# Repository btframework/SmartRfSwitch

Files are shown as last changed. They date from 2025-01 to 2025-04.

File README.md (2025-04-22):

# Smart RF Switch

 **Required Hardware**
 - 433Mhz RF switch and relay set
 - ESP32C4FN Super Mini
 
 **Required Arduino Libraries**
 - esp32 by Espressif Systems (board) 3.2.0
 - HomeSpan 2.1.1
 
 **Arduino IDE Settings**
 - Board: ESP32C3 Dev BModule
 - ESP CDC On Boot: Enabled
 - CPU Frequency: 80MHz (WiFi)
 - Core Debug Level: None
 - Erase All Flash Before Sketch Upload: Disabled
 - Flash frequency: 80Mhz
 - Flash Mode: QIO
 - Flash Size: 4MB (32Mb)
 - JTAG Adapter: Disabled
 - Partition Scheme: Huge APP (3MB No OTA/1MB SPIFFS)
 - Upload Speed: 921600
 - Zigbee Mode: Disabled
 - Programmer: Esptool

This repository contains firmware for the HomeKit device described in [this video](https://youtu.be/C4awq37Im1w).

## 433Mhz RF Switch to HomeKit connection
   
  Smart light bulbs, smart relays, and other “smart” devices in the home are cool. But! There's always that damn “but.” At 3 a.m., when everyone is asleep, yelling, “Hey Siri! Turn on the kitchen light” is not a good idea. And constantly reaching for your smartphone to turn something on or off is also not a good idea. You can, of course, put motion sensors in, but there are nuances with them. So you can't do without switches.

  My first impulse was to buy a switch that is compatible with my smart home system (and I have an Apple Home, mind you). I looked at what was on sale. First of all, most are from the Chinese and required their own application that somehow cleverly threw something there somewhere. Secondly, which is quite sad, most required a prepared wiring or ZigBee gateway, or both. In general, the option fell away for several reasons.

  The second thought (which comes later) was to buy any switch at all and wire it to the Apple Home via HomerBridge. This idea again ran into ZigBee hubs and wiring.

  Having given up on all this nonsense and racking my brains, I suddenly remembered that I'm a programmer. What should we do to make a switch ourselves? No problem. We take a radio relay and build it. I stalled on the fact that I was too lazy to print a normal switch button. So the idea was put aside in not a very long.

  So, not too long ago, I was looking for something online and decided to see what's out there in the smart switch technology realm. And I found a cool thing: a full-size switch with a relay on 433 MHz. And the main thing is that this switch (the button itself) works from a battery, and the relay is connected to the wires of the chandelier (or bulb). Thus, special wiring for it is not needed.

  > Let me make it clear: by “special wiring”, I mean phase and zero wiring to the light switch. That is, you should have three wires coming to the switch: phase from the switchboard (which is broken), phase to the chandelier, and zero from the switchboard. Usually, the standard wiring to the switch is just two wires: phase from the switchboard, and it goes to the chandelier (phase break). There is no zero there.

  Here is the switch.

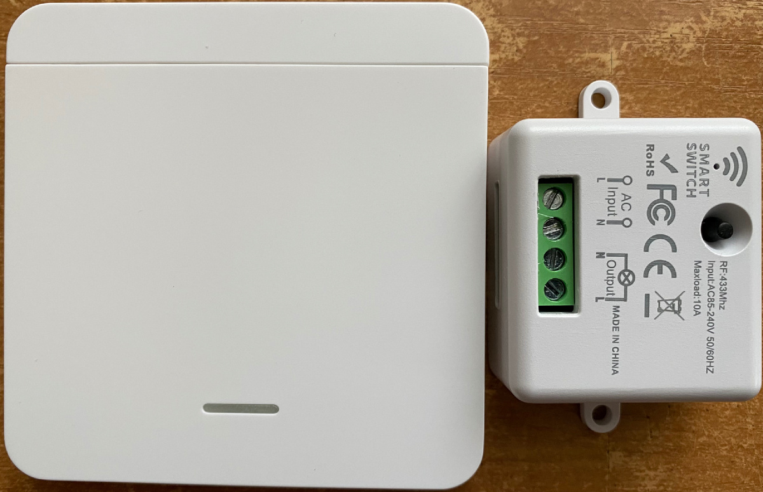
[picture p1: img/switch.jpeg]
RF Switch
  

  The only thing left to do is to make this switch compatible with Apple Home. Naturally, I will use the ESP32 in conjunction with the Arduino HomeSpan library. I have been friends with this library for a long time, and I already have devices made on its basis. Yes, and the experience of the “adaptation” radio call (also on 433) I already had. No problems were expected.

  Before breaking the relay, I looked in the manual. And there I found a mention that more than one button can be attached to the relay. Interesting, I thought, so the buttons are different somehow. Well, it's time to open this marvelous device of Chinese industry. The button is of little interest to me; it's just an ordinary RF transmitter. It works, and it's good. But the relay should be studied in detail. The case is not glued, not sealed, and in general, it opens easily. Here's what I got out of this white box.

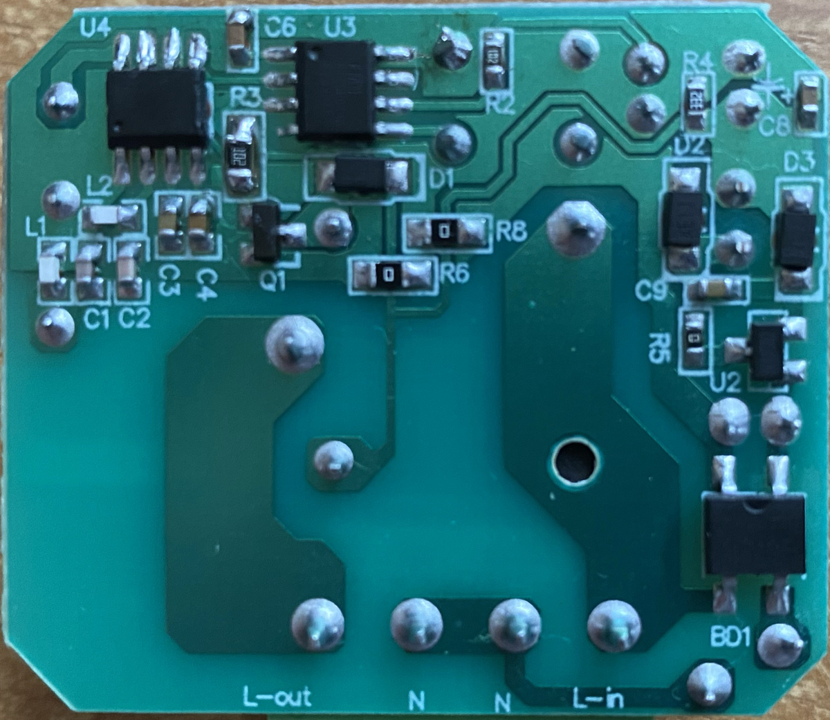
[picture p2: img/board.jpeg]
RF Switch Board
  

  In the right part of the board, you can see a transformerless (you should take note of it!) power supply assembled on diode bridge BD1. Some microcircuit U2 (I suspect it is a stabilizer for some volts) with marking IVAP302 (couldn't find what it is; if you know what it is, please write in comments), diodes D2 and D3, and some stuff (capacitors, resistors). Several elements are not labeled and soldered on the back side of the board. In particular: a ballast resistor and a couple of smoothing capacitors. All in all, nothing interesting. The only thing that interested me here is the stabilizer. Since it determines the supply voltage of the rest of the circuit and, as a consequence, the options for matching it (the circuit) with ESP32. You can stupidly measure the output voltage from the power supply, and then you can figure it out by indirect signs. I decided on the second option because I still need to find out the “protocol” of communication between the button and the relay.

  In the left part of the board there is the relay control circuit itself, consisting of two microcircuits, U4 (the name is lost) and U3 (marking FMD FT60E011A F269RKE), some loose parts, transistor Q1, and, actually, the relay itself. Relay marking: BRD-SS-105LMF. And this indicates that the relay is a five-volt relay. Which is very good and hints that the circuit works from 5 volts. Of course, it is not certain that the rest of the circuit is powered by five volts, since the relay is switched through a transistor, but it is something. It's unlikely to be more than that.

  A quick Google search for FT60E011A gives us a link to a data sheet that shows that this is a simple microcontroller. This is also indicated by the fact that to this chip (U3) are connected the button, the LED, the base of transistor Q1 (via current-limiting resistor R3), and the second chip (U4). Hence, U4 is an RF chip. And it transmits the received signal to the microcontroller. In this case I am not interested in the RF chip itself and its piping, so I will not describe what is there and how. It's just a bunch of capacitors and an antenna.

  > Transistor Q1 in this circuit works as a key: it allows a small current from the microcontroller to control a relatively large relay winding current. Usually microcontroller outputs are designed for currents of a couple of tens of milliamperes. But the relay itself consumes much more current (it can even reach hundreds of milliamperes). The microcontroller will simply not be able to deliver such current to its outputs. And if it can, it is very likely to burn out. This is why a transistor key is used. Well, diode D1 dampens the reverse energy discharge from the relay coil.

  Now I need to figure out what exactly the RF chip sends to the microcontroller and how the microcontroller controls the relay. I'll look at the signal levels as well. It's time to poke around with an oscilloscope.

  Before poking with oscilloscope probes, we should solve the problem with the power supply. I don't really want to get into the device, which is directly powered from 220 without isolation. I decided to supply power directly after the diode bridge from a laboratory power supply unit. It started from 12 volts.

  Signal from the RF chip to the IC without a button command. Occasionally there's some interference. But it's mostly quiet.

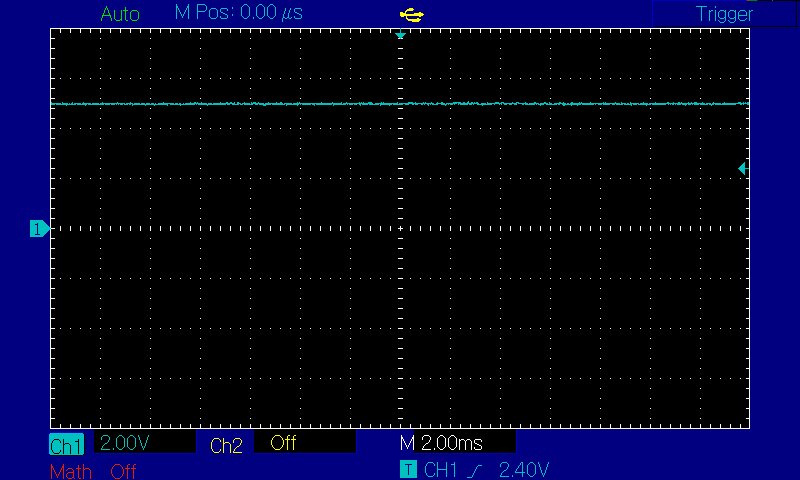
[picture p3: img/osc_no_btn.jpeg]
Oscillogram without button pressed
  

  If you press the button, the RF chip starts transmitting something to the microcontroller. I suspect it is the code of the button.

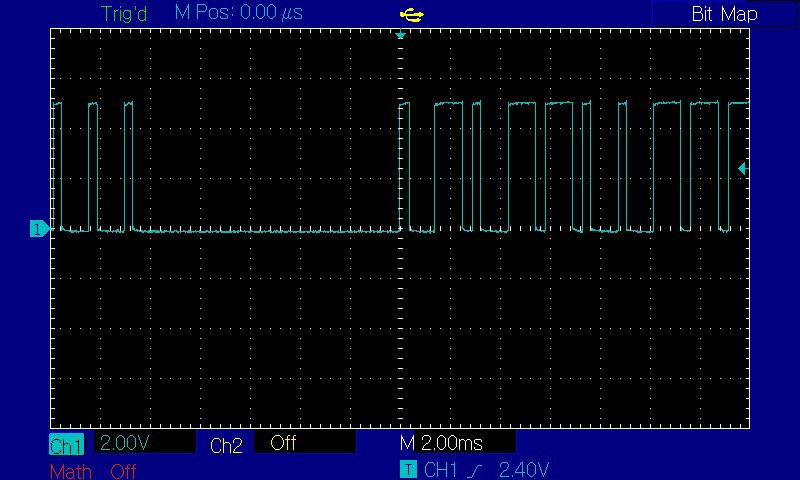
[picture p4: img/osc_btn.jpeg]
Oscillogram with button pressed
  

  The screenshot doesn't show everything, but it's a pretty long sequence. You can immediately see that the signal has a 5-volt level, which is very, very good. Well, and the relay is 5 volts, as I mentioned above. So there will be no problems with level matching.

  I didn't really want to decode and emulate the signal, so I also looked at the relay control signal (on R3 on the microcontroller side). I will not give the oscillogram; everything is expected there. Either constantly high level (5 volts) when the relay is turned on (closes the output contacts). Or constantly low when the output is open.

  In general, I decide to connect to the gap between the microcontroller and Q1. To do this, it will be necessary to unsolder resistor R3. I have sketched this connection diagram.

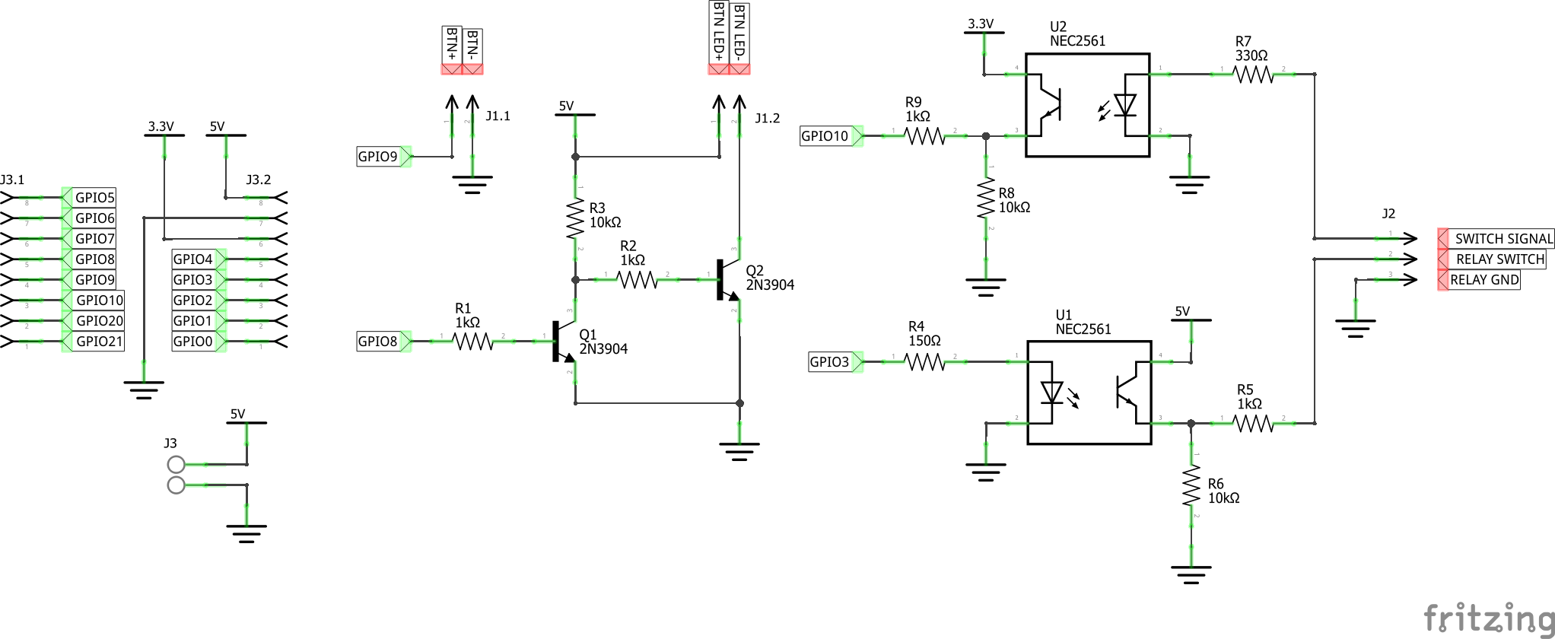
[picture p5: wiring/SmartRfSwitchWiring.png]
Wiring diagram
  

  According to the scheme, everything is very simple. Opto isolation from the relay (since I remember that there is a transformerless power supply, which has no galvanic isolation from the 220-volt network). Switch The signal is soldered to the microcontroller output, which goes to the top pin of R3. Relay switch—to the lower pin of resistor R3 (which is soldered out), to the base of transistor Q1. And the ground to any “-” point on the relay board. There is a very convenient one next to R2. BTN+ and BTN-: Here you can connect an external button to control ESP32 (for details see the HomeSpan help). BTN LED+ and BTN LED- are the indicator LEDs. I have a button with a built-in LED, which is very convenient. Again, refer to the HomeSpan help for details.

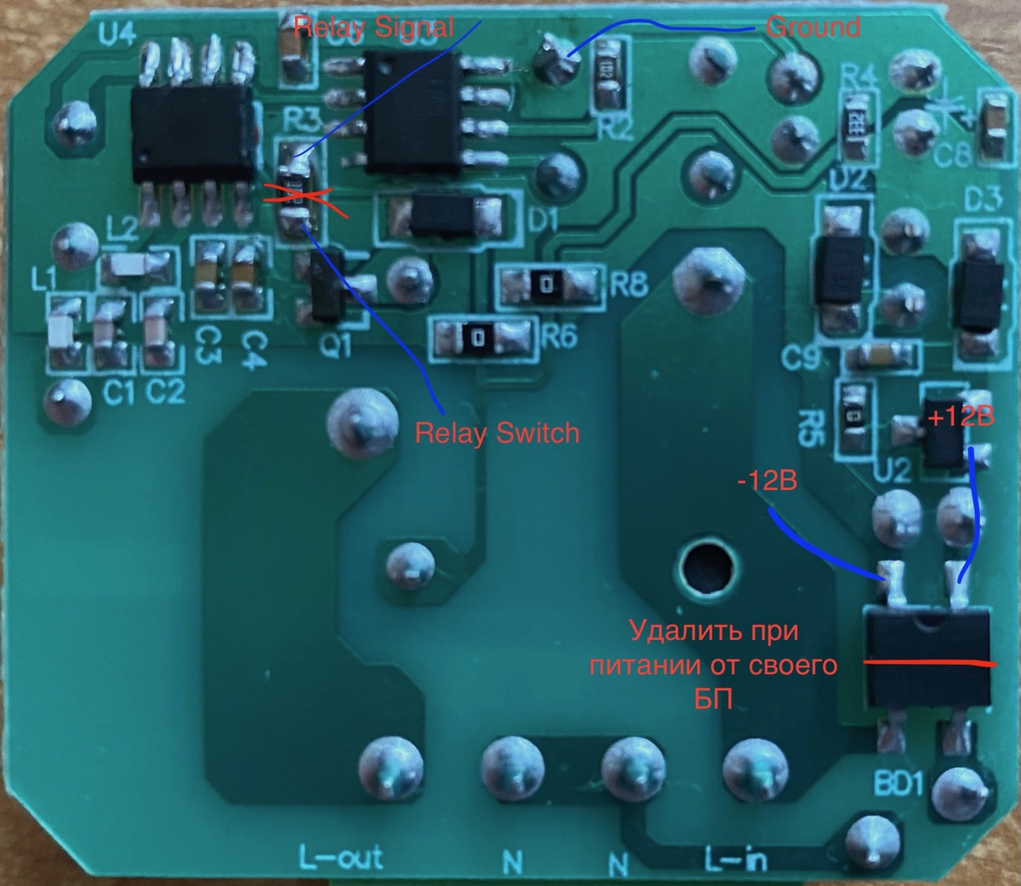
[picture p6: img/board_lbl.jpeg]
Board with labels
  

  There is only one problem left: the ESP32 power supply. The initial idea to power everything from a single 5 volt power supply has failed so far, because the stabilizer starts only from 12 (or rather, the power supply circuit starts from 12, the stabilizer would probably start from 6). It is possible, of course, to supply power directly, bypassing the entire power supply circuit, but, frankly speaking, I did not want to unsolder a lot of parts. I wanted to leave the possibility to quickly reset the relay.

  > If you want to power the relay from your own power supply, then 12 volts should be supplied to the output (upper on the photo) contacts of the diode bridge (BD1). The left one is “+,” the right one is “-.” The diode bridge must be soldered out! The circuit consumes less than 100 milliamperes when powered from 12 volts.

  I decided to leave the relay power supply as it is and use a separate 5-volt power supply to power the ESP32. Thus, I will only need to remove resistor R3 and solder three wires.

  Important point! It is necessary that the power supply used is completely galvanically isolated from the 220 network. Otherwise, all the white smoke will come out very quickly. Fortunately, I have such a PSU.

  In general, everything is thought out—solder. I didn't bother much with the board layout. Then I printed the box and connected the button. Here it is, all assembled.

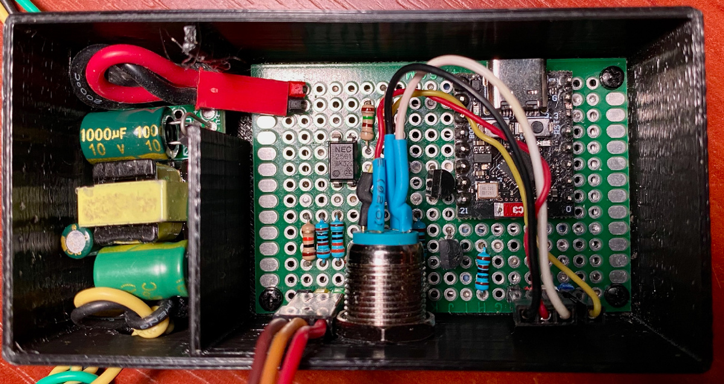
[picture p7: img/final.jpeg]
All in the box
  

  I've got the electrics and electronics sorted out. It's time to prepare the firmware. Well, there are no special problems with it. The logic is quite simple: since the control signal has a logic level and is constant for a given state (always 5V if the relay is on and always 0V if the relay is off), the optimal solution is to use interrupts on the change of signal level. It doesn't matter what the relay MC outputs. What matters is when that signal changes. You can tell by the signal change that the button was pressed. And what actually needs to be done with the relay (on or off) depends solely on the internal state of the ESP32 firmware. This allows the relay to be controlled independently of the current state of the control signal, either by the button or from Apple Home.

  **Support the project**
  
  If you like the project you can support me by the following link:
  
  **BTC**: bitcoin:1A1WM3CJzdyEB1P9SzTbkzx38duJD6kau  
  **BCH**: bitcoincash:qre7s8cnkwx24xpzvvfmqzx6ex0ysmq5vuah42q6yz  
  **ETH**: 0xf780b3B7DbE2FC74b5F156cBBE51F67eDeAd8F9a  
  
  **Boosty**: https://boosty.to/drone_tales/donate  
  **BuyMeACoffee**: https://buymeacoffee.com/dronetales

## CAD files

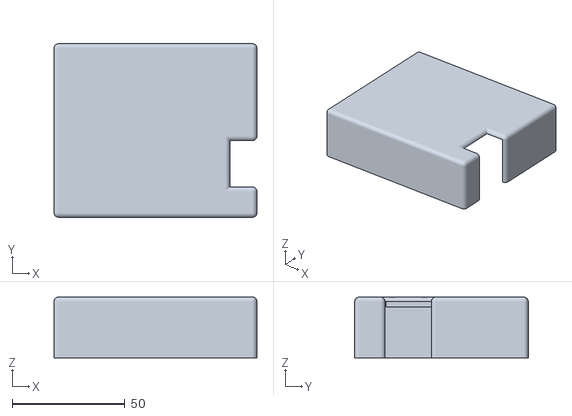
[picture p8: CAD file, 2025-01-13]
3d models/RfSwitchTopCase.stl
90.0 x 77.0 x 27.0

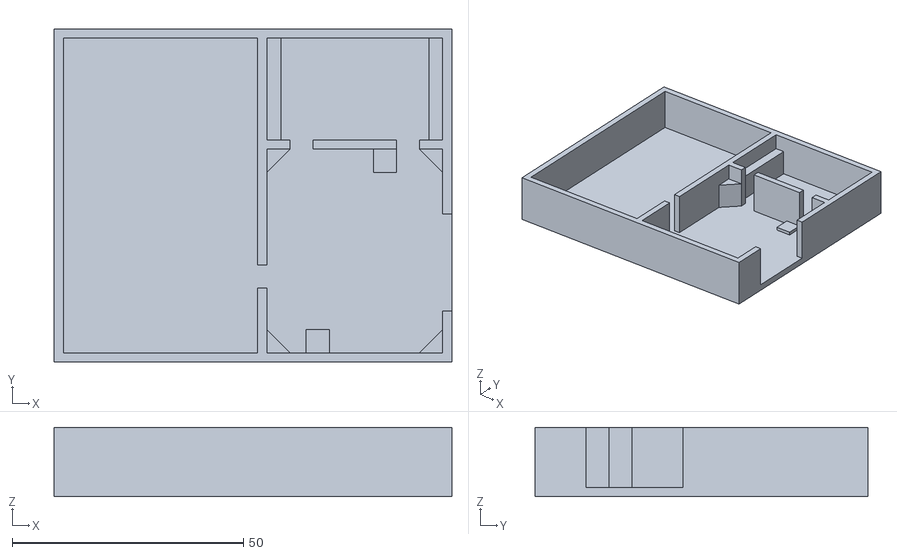
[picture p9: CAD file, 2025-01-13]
3d models/RfSwitchCase.stl
86.0 x 72.0 x 15.0

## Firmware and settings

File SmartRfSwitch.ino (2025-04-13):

// ESP32C3FN4 SuperMini Board
// ===============================================================
// Arduino IDE settings:
//   - Board: ESP32C3 Dev Module
//   - ESP CDC On Boot: Enabled
//   - CPU Frequency: 80MHz (WiFi)
//   - Core Debug Level: None
//   - Erase All Flash Before Sketch Upload: Disabled
//   - Flash frequency: 80Mhz
//   - Flash Mode: QIO
//   - Flash Size: 4MB (32Mb)
//   - JTAG Adapter: Disabled
//   - Partition Scheme: Huge APP (3MB No OTA/1MB SPIFFS)
//   - Upload Speed: 921600
//   - Zigbee Mode: Disabled
//   - Programmer: Esptool
// ===============================================================

#include <HomeSpan.h>


/**************************************************************************************/
/*                                        Pins                                        */

#define STATUS_LED_PIN      GPIO_NUM_8
#define CONTROL_PIN         GPIO_NUM_9

#define SWITCH_SIGNAL_PIN   GPIO_NUM_10
#define SWITCH_CONTROL_PIN  GPIO_NUM_3

/**************************************************************************************/


/**************************************************************************************/
/*                                  HomeSpan sensors                                  */

bool LampState = false;
bool CurrentLampState = false;

struct RfSwitchingLamp : Service::LightBulb
{
    SpanCharacteristic* FPower;
    
    RfSwitchingLamp() : Service::LightBulb()
    {
        FPower = new Characteristic::On();
    }
    
    bool update()
    {
        LampState = FPower->getNewVal();
        CurrentLampState = LampState;
        digitalWrite(SWITCH_CONTROL_PIN, LampState);
        return true;
    }
};

/**************************************************************************************/


/**************************************************************************************/
/*                                 Arduino  rountines                                 */

RfSwitchingLamp* Lamp;

void IRAM_ATTR SwitchSignalInterrupt()
{
    LampState = !LampState;
}

// Arduino initialization routine.
void setup()
{
    // Initialize debug serial port.
    Serial.begin(115200);

    // Initialize pins.
    pinMode(STATUS_LED_PIN, OUTPUT);
    pinMode(CONTROL_PIN, INPUT);

    pinMode(SWITCH_SIGNAL_PIN, INPUT);
    pinMode(SWITCH_CONTROL_PIN, OUTPUT);

    // Turn all output pins off.
    digitalWrite(STATUS_LED_PIN, HIGH);
    digitalWrite(SWITCH_CONTROL_PIN, LOW);

    // Initialize HomeSpan.
    homeSpan.setControlPin(CONTROL_PIN);
    homeSpan.setStatusPin(STATUS_LED_PIN);
    homeSpan.setPairingCode("63105322");
    homeSpan.begin(Category::Lighting, "DroneTales RF Switching Lamp");

    // Build device's serial number.
    char Sn[24];
    snprintf(Sn, 24, "DRONETALES-%llX", ESP.getEfuseMac());

    // Configure device.
    new SpanAccessory();
    new Service::AccessoryInformation();
    new Characteristic::Identify();
    new Characteristic::Manufacturer("DroneTales");
    new Characteristic::SerialNumber(Sn);
    new Characteristic::Model("DroneTales RF Switching Lamp");
    new Characteristic::FirmwareRevision("1.0.0.0");
    Lamp = new RfSwitchingLamp();

    // Attach remote control interrupt.
    attachInterrupt(SWITCH_SIGNAL_PIN, SwitchSignalInterrupt, CHANGE);
}

// Arduino main loop.
void loop()
{
    if (CurrentLampState != LampState)
    {
        CurrentLampState = LampState;
        Lamp->FPower->setVal(CurrentLampState);
        digitalWrite(SWITCH_CONTROL_PIN, LampState ? HIGH : LOW);
    }

    homeSpan.poll();
}

/**************************************************************************************/

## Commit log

2025-01-11 Case model files
    [RfSwitchCase.stl, RfSwitchTopCase.stl]
2025-01-13 file organization
    [RfSwitchCase.stl, RfSwitchTopCase.stl, SmartRfSwitch.fzz]
